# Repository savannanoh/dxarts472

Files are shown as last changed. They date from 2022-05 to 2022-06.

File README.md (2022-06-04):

# dxarts472

## Final

### Summary

My project consists of three nature-inspired robots in a habitat that has familiar objects from nature, as well as exposed electronic components. The robots mimic mushrooms and have a mechanism that makes them open and close like umbrellas. Inspired by the fact that mushcrooms, trees, and other things in nature communicate via electrical signals, they have antennas on them that pick up electromagnetic signals from the outlets that are powering them, each other, and things in the environment. What the antennas pick up controls how quickly they move. Since the movements of the robots affect the electromagnetic signals, this causes a feedback loop. Each robot has a light sensor that is meant to detect when someone is in front of the robot, presumably watching it. When it detects someone, the robot stops moving. This makes the piece a sort of anti-installation, showing that while nature and the things around us are speaking to each other, they are not speaking to us, they are not performing for us, and we are simply eavesdroppers. 

### Materials 

Each of the robots consists of the following:
- Arduino Uno
    - Link to code file is below under "Relevant Files"
- Bipolar stepper motor
- Power adapter for powering the Arduino as well as the motor
- L293D IC stepper motor driver
    - I followed this tutorial for wiring the driver: https://lastminuteengineers.com/stepper-motor-l293d-arduino-tutorial/
- Photoresistor
    - Used for detecting the presence of a person
- Button
    - Used for switching the direction of the motor. Since the motors all move at different speeds, when I stop the robots I cannot guarantee where they are in their opening or closing, the button allows me to switch directions so they don't break going too far open or too far closed
- Fabric antenna
- Fabrc cover
- Umbrella mechanism
    - Sticks x6
        - Heat shrink x3
        - Bamboo skewers, cut x4
    - 3D printed threaded rod
    - 3D printed threaded nut with holes
    - 3D printed nut with holes
    - Pieces of thick wire for constraining threaded nut from rotating x3

    The robots open and close by a custom-made mechanism. The main idea is that the motor is attached to a threaded rod, which has a threaded nut that can rotate and go up and down the rod. By constraining the nut from rotating it will go up and down as the motor rotates. A non-threaded nut is attached to the tops of the wires constraining the threaded nut and sits in the same orientation. The top and bottom nuts both have six holes around the center, and this is where the sticks are attached. Each stick is made up of four pieces of cut bamboo skewer, attached with three pieces of heat shrink. Once the sticks are attached to the nuts, when the motor rotates, the threaded nut moves up and down and the sticks bend outwards and straighten, and when the fabric is attached, this makes the fabric open and close like an umbrella. 

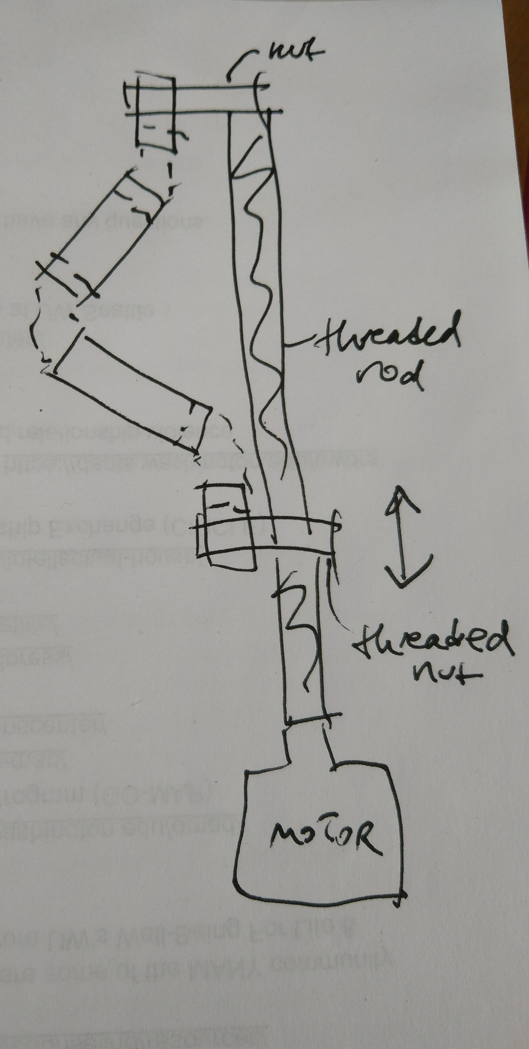
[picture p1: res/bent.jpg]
bent
    
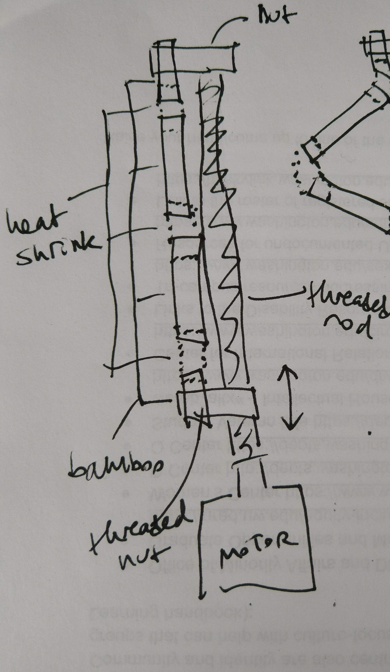
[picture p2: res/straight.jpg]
straight
    

    Here is a video where you can see the mechanism working: https://github.com/savannanoh/dxarts472/blob/main/videos/draft.mp4

### Exhibition

exhibit image

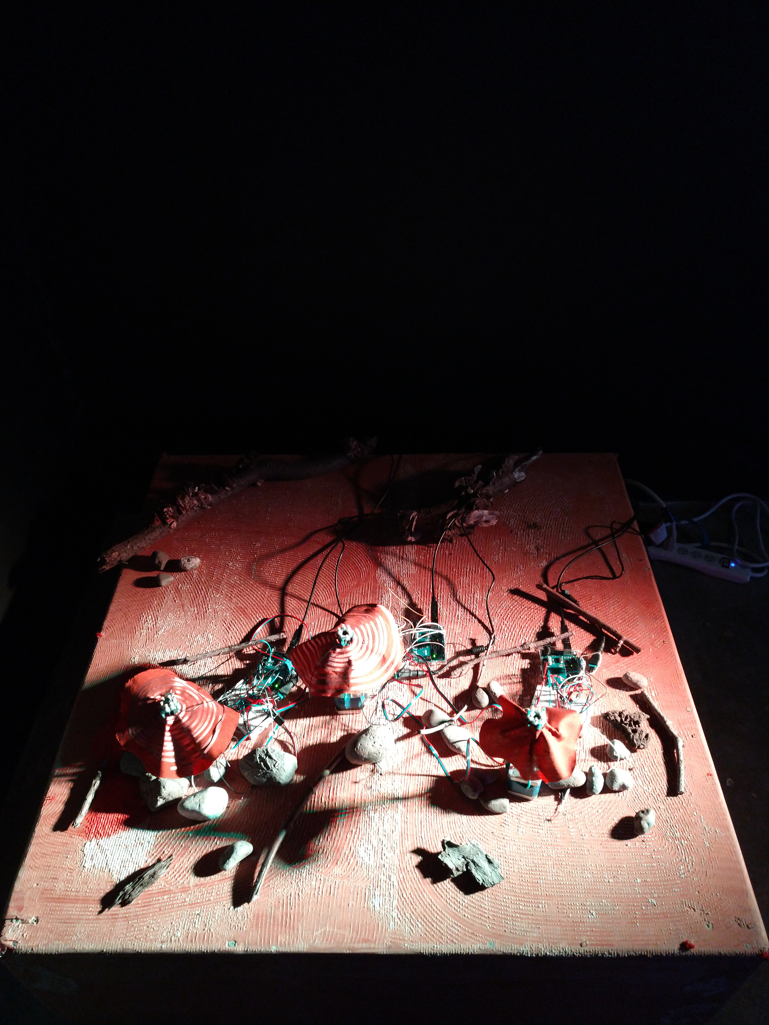
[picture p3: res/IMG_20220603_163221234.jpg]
exhibit image


Videos:
https://github.com/savannanoh/dxarts472/blob/main/videos/exhibit1.mp4
https://github.com/savannanoh/dxarts472/blob/main/videos/exhibit2.mp4

### Relevant Files

Arduino code for the exhibition: https://github.com/savannanoh/dxarts472/blob/main/exhibition.ino

Rod model: https://github.com/savannanoh/dxarts472/blob/main/many%20rods.stl

Nut model: https://github.com/savannanoh/dxarts472/blob/main/bigger%20holes2.stl

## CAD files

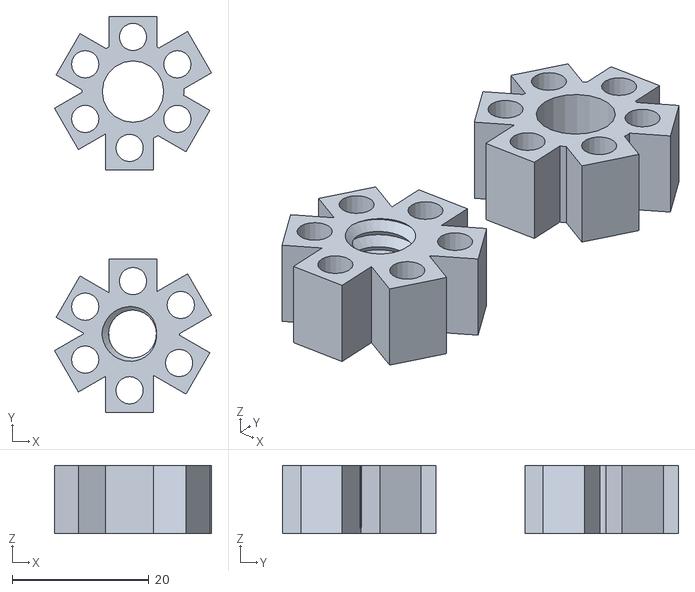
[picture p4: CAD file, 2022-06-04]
bigger holes2.stl
23.0 x 58.0 x 10.0

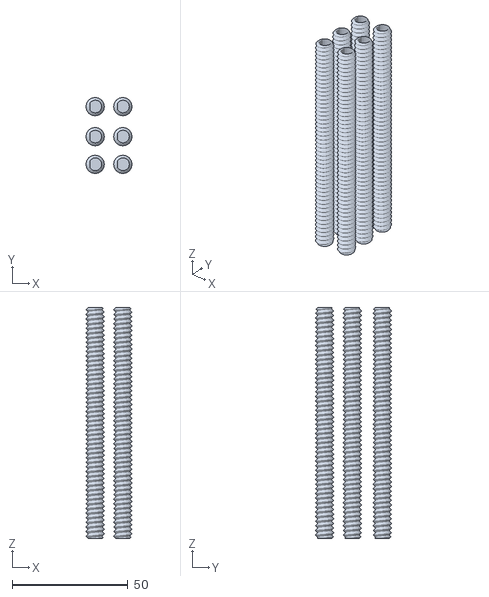
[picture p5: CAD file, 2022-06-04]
many rods.stl
20.0 x 33.0 x 100.0

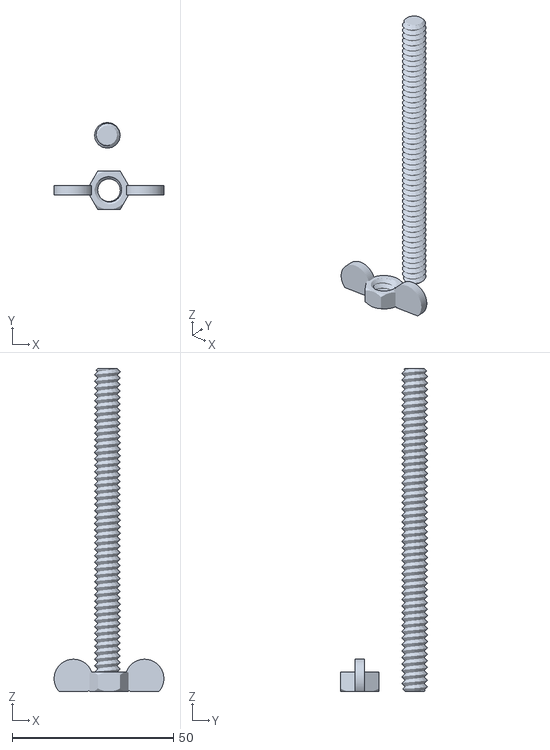
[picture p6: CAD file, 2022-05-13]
hex nut and threaded rod.stl
34.0 x 27.0 x 100.0

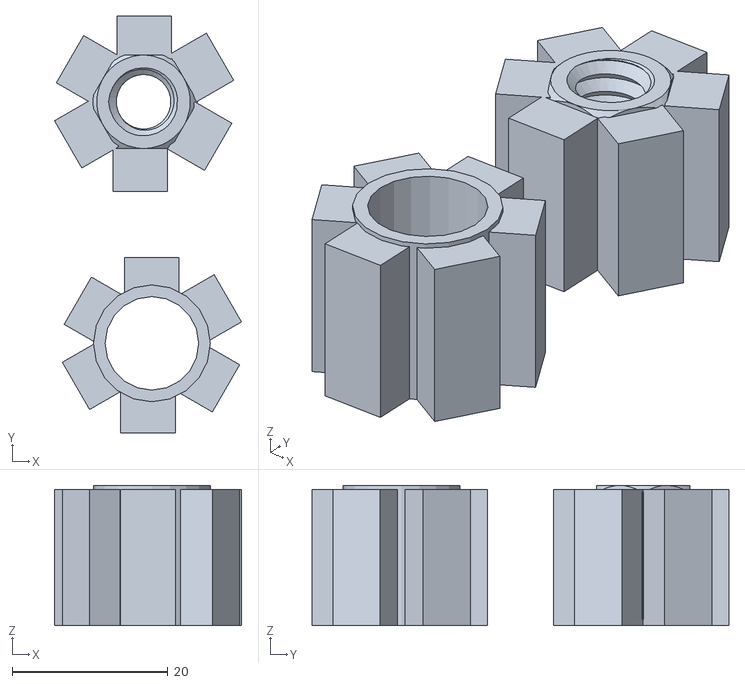
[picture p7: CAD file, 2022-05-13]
Flower nut only (2).stl
24.0 x 53.5 x 18.0

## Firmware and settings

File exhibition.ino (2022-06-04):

//button is for switching direction so that the robot does not stretch or squish too much
#define BUTTON_PIN 2 
#define ANTENNA_PIN A0
#define LIGHT_PIN A1

// Include the Arduino Stepper Library
#include <Stepper.h>

const int max_speed = 120;
const int min_speed = 20;
const int proxim = 90; //calibrated based on the environment

// Number of steps per output rotation
const int stepsPerRevolution = 200;
const int limit = 3000;
int stepped = 0;
int dir = 1;
int ant = 0;
int dist = 0;

// Create Instance of Stepper library
Stepper myStepper(stepsPerRevolution, 12, 11, 10, 9);

void setup()
{
  pinMode(BUTTON_PIN, INPUT);         
  myStepper.setSpeed(80);
  // initialize the serial port:
  Serial.begin(9600);
}

void loop() 
{
  ant = analogRead(ANTENNA_PIN)/2;
  Serial.print("antenna = ");
  Serial.println(ant);
  Serial.println(stepped);
  Serial.print("light = ");
  dist = analogRead(LIGHT_PIN);
  Serial.println(dist);

  if(ant < min_speed) {
    myStepper.setSpeed(min_speed);
  } else if(ant > max_speed) {
    myStepper.setSpeed(max_speed);
  } else {
    myStepper.setSpeed(ant);
  }

  if (digitalRead(BUTTON_PIN)) {       
    Serial.println("pressed");
    delay(40);                        
    while (digitalRead(BUTTON_PIN));
    dir *= -1;
    stepped = 0;
    delay(200);
  } else {
    if(dist >= proxim) {
      if(stepped < limit) {
        myStepper.step(stepsPerRevolution * dir);
        stepped += stepsPerRevolution;
      } else {
        dir *= -1;
        stepped = 0;
        delay(200);
      }
    }
  }
}

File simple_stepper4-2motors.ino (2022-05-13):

// Include the Arduino Stepper Library
#include <Stepper.h>

// Number of steps per output rotation
const int stepsPerRevolution = 400;

// Create Instance of Stepper library
Stepper myStepper(stepsPerRevolution, 12, 11, 10, 9);
Stepper myStepper2(stepsPerRevolution, 7, 6, 5, 3);


void setup()
{
  // set the speed at 20 rpm:
  myStepper.setSpeed(20);
  myStepper2.setSpeed(20);
  // initialize the serial port:
  Serial.begin(9600);
}

void loop() 
{
  // step one revolution in one direction:
  Serial.println("clockwise");
  myStepper.step(stepsPerRevolution);
  myStepper2.step(stepsPerRevolution);
  delay(500);

  // step one revolution in the other direction:
  Serial.println("counterclockwise");
  myStepper.step(-stepsPerRevolution);
  myStepper2.step(-stepsPerRevolution);
  delay(500);
}

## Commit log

2022-05-13 added stepper code files
2022-05-13 Added stl file for special hex nut
    [Flower nut only (2).stl]
2022-05-13 Added original hex nut and threaded rod file
    [hex nut and threaded rod.stl]
